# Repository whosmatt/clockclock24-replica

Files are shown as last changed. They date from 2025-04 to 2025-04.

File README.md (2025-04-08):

# clockclock24-replica
DISCLAIMER: All files in this repository are intended for personal use only. All design rights go to Humans Since 1982.

Simple mechanical design for a clockclock24 wall clock compatible with the PCB design by [Vallasc](https://github.com/Vallasc), available here: [clockclock24-replica](https://github.com/Vallasc/clockclock24-replica)  

[3D Preview](clockclock24%20body%20(preview).stl)

## Body
The body is CNC-Milled from a 900x400mm board of 19mm MDF. A frame for wall-mounting and LED ambient lighting is constructed from the same 19mm MDF, cut into different-length strips. The frame is assembled and attached using regular wood glue. 

## PCB attachment
The assembled PCBs are attached using 4 identical 3D-printed spacers each, designed for an ST (self-tapping) 2.9 x 16 metric screw. When using the specified screw, the spacers will self-align the PCBs to the wooden body. 

## Clock arms
The clock arms are 3D-printed and designed to press-fit onto the motor shaft. Slight adjustments to the bore size may be needed to adjust for 3D-printer tolerances. 

## Parts list
| Qty. | Desc. | Stock | Processing |
|-----:|---|---|---|
| 1 | Body | 900x400x19mm MDF  | CNC milling (both sides) |
| 2 | Frame piece (long) | 838x25x19mm MDF | Wood glue |
| 2 | Frame piece (short) | 300x25x19mm MDF | Wood glue |
| 32 | ST 2.9 x 16 metric screw | | |
| 32 | [Spacer](drawings/clockclock24%20spacer.stl) | PLA or comparable | 3D-printing |
| 24 | [Upper hand](drawings/clockclock24%20upper%20hand.stl) | PLA or comparable | 3D-printing |
| 24 | [Lower hand](drawings/clockclock24%20lower%20hand.stl) | PLA or comparable | 3D-printing |

## Photos
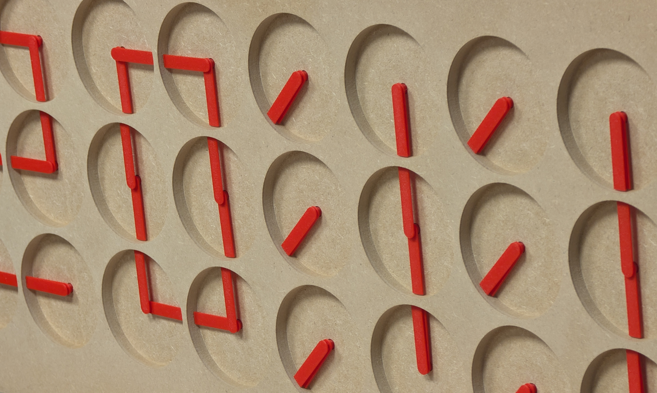
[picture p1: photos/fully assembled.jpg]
Front face of the fully assembled clock

Front face of the clock without arms
Back face of the clock during assembly, with visible spacers
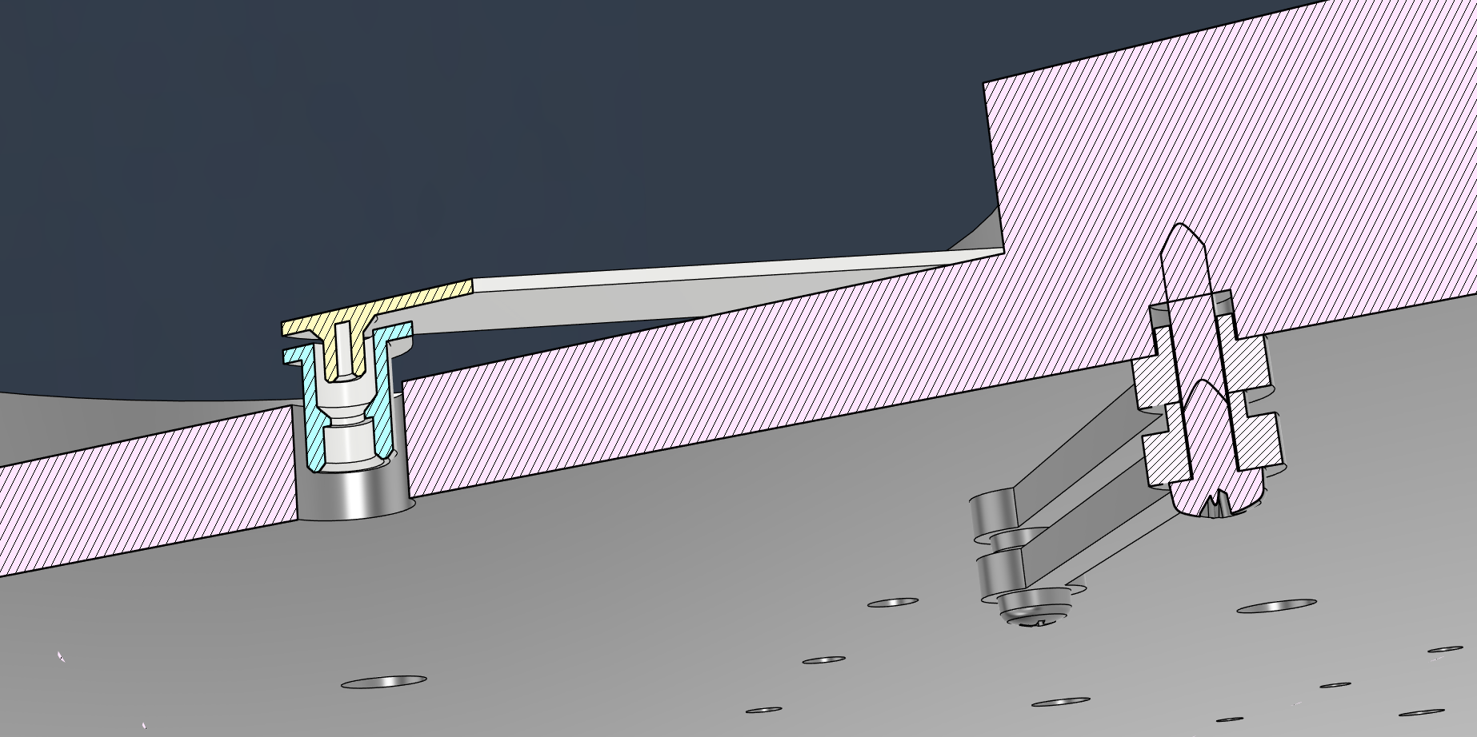
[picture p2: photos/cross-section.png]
Cross section of the clock, showing internal construction of the arms and spacers


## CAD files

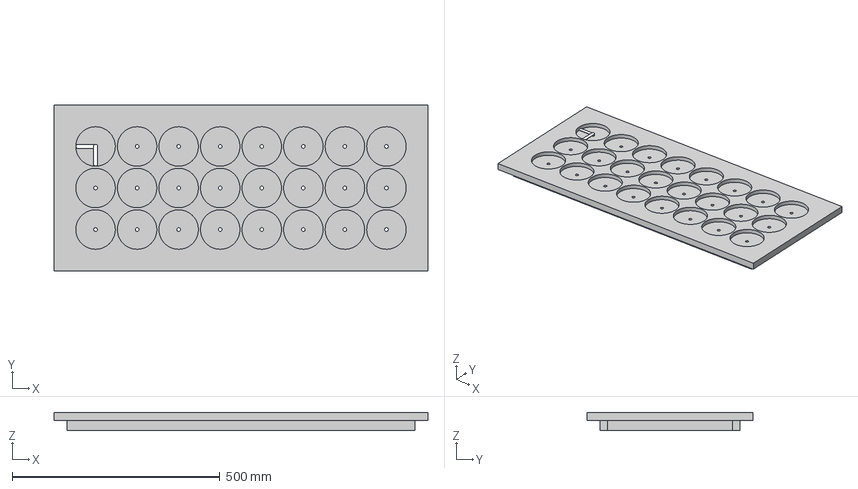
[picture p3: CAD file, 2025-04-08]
drawings/clockclock24 full v14.step
900.0 x 400.0 x 44.0 mm
stepper axle
upper hand
lower hand
spacer x 2
DIN EN ISO 7049 - ST 2.9 x 16 - C - H Steel 4.6 Plain x 2
DIN EN ISO 7049 - ST 2.9 x 6.5 - C - H Steel 4.6 Plain x 2

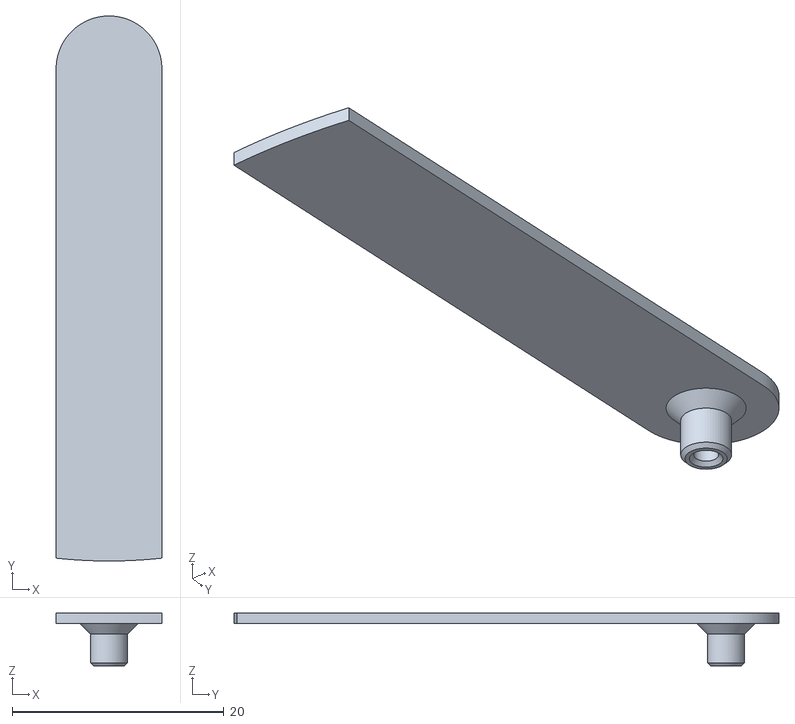
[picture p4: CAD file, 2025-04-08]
drawings/clockclock24 upper hand.stl
10.0 x 51.5 x 5.00

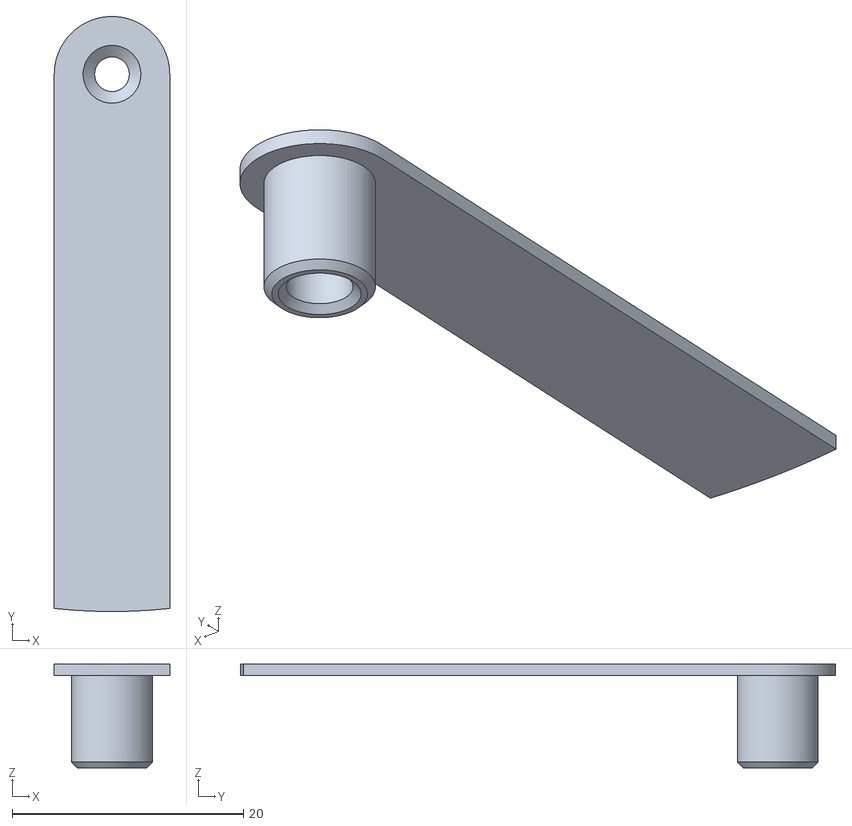
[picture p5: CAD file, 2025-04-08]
drawings/clockclock24 lower hand.stl
10.0 x 51.5 x 9.00

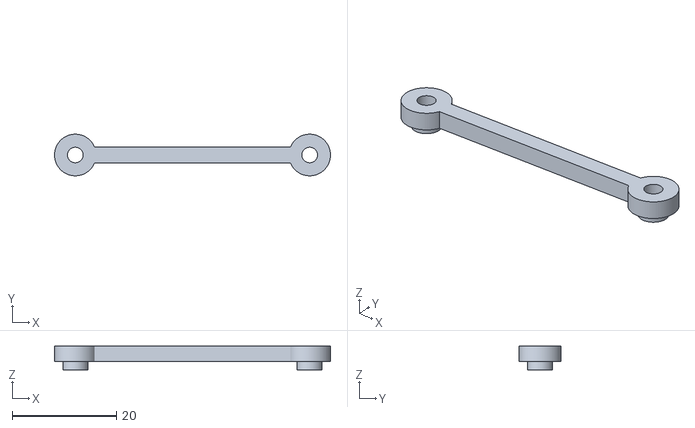
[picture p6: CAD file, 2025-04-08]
drawings/clockclock24 spacer.stl
53.0 x 8.00 x 4.60

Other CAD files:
clockclock24 body (preview).stl
drawings/clockclock24 body Drawing v4 AutoCAD.dwg
drawings/clockclock24 body Drawing v4 Simplified.dwg

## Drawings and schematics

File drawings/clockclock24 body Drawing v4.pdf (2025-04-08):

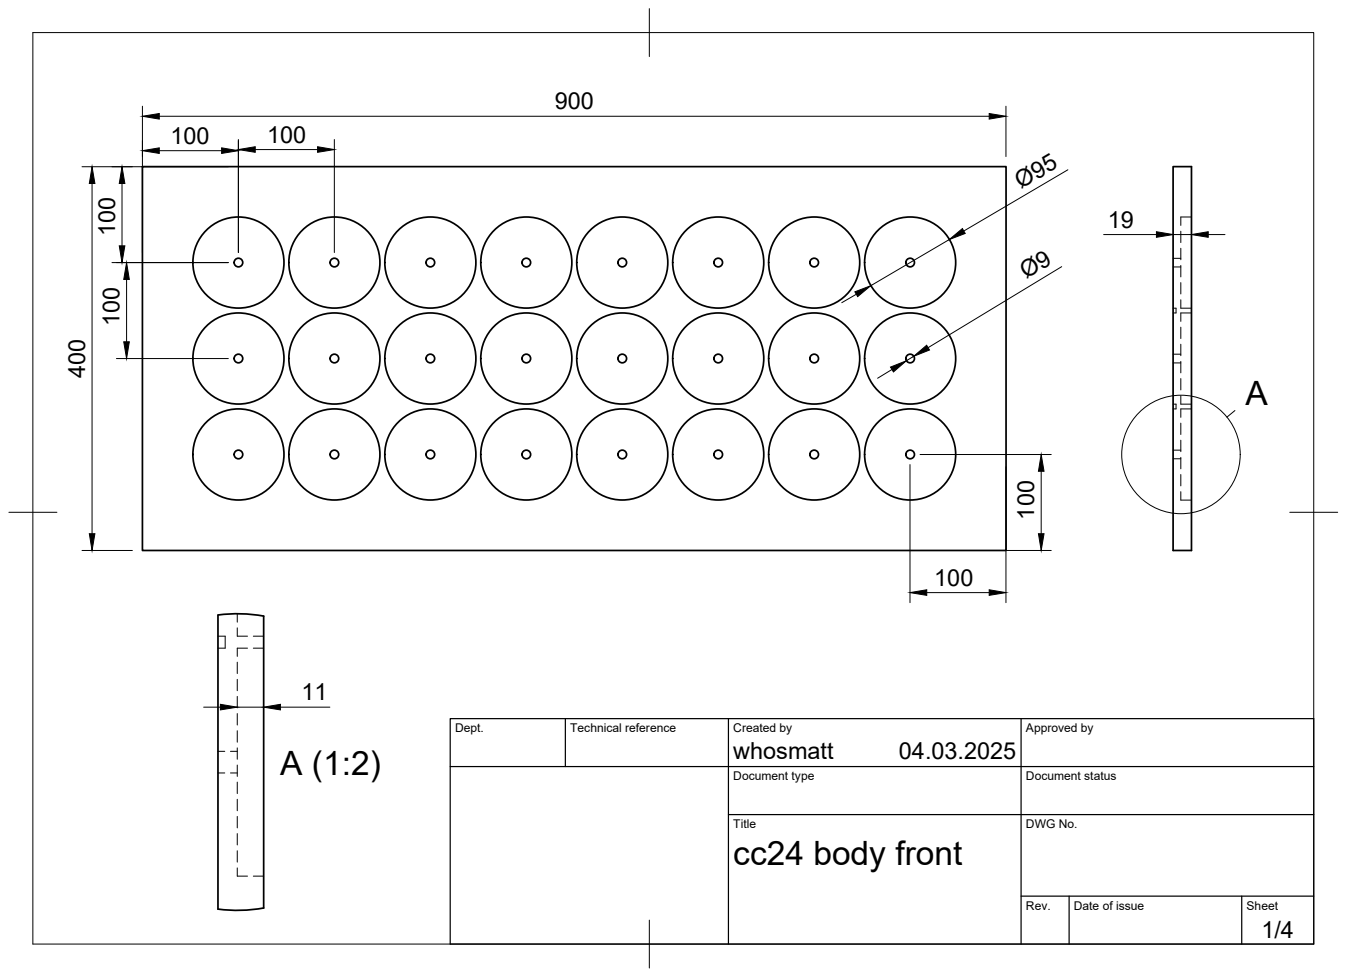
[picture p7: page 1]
whosmatt 400

Dept. | Technical reference | Created by 04.03.2025 | Approved by

Document type | Document status

Title cc24 body front | DWG No.

Rev. | Date of issue | Sheet

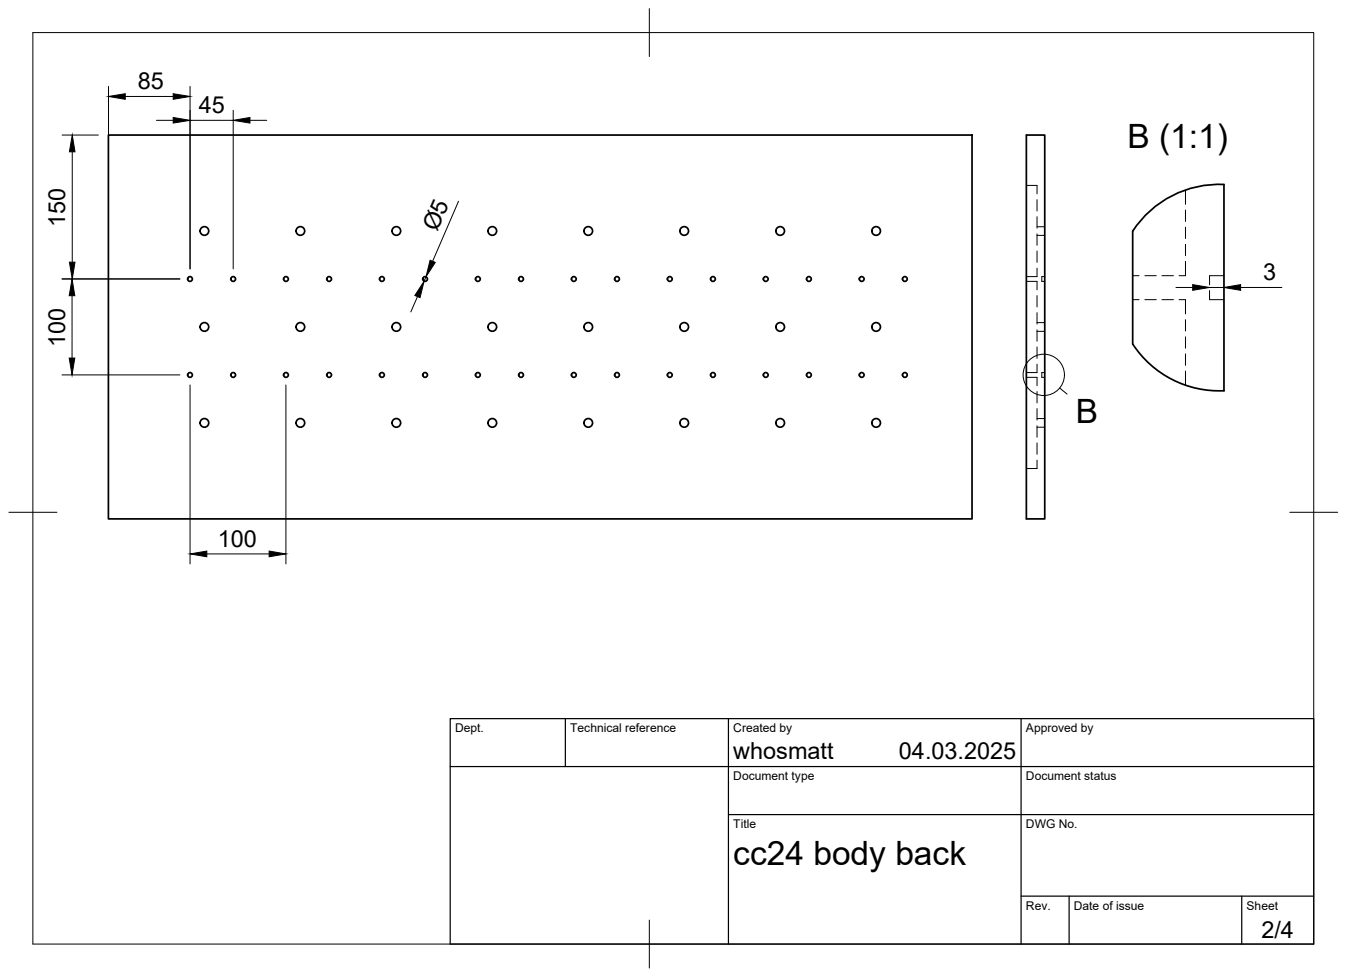
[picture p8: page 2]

Dept. | Technical reference | Created by whosmatt 04.03.2025 | Approved by

Document type | Document status

Title cc24 body back | DWG No.

Rev. | Date of issue | Sheet

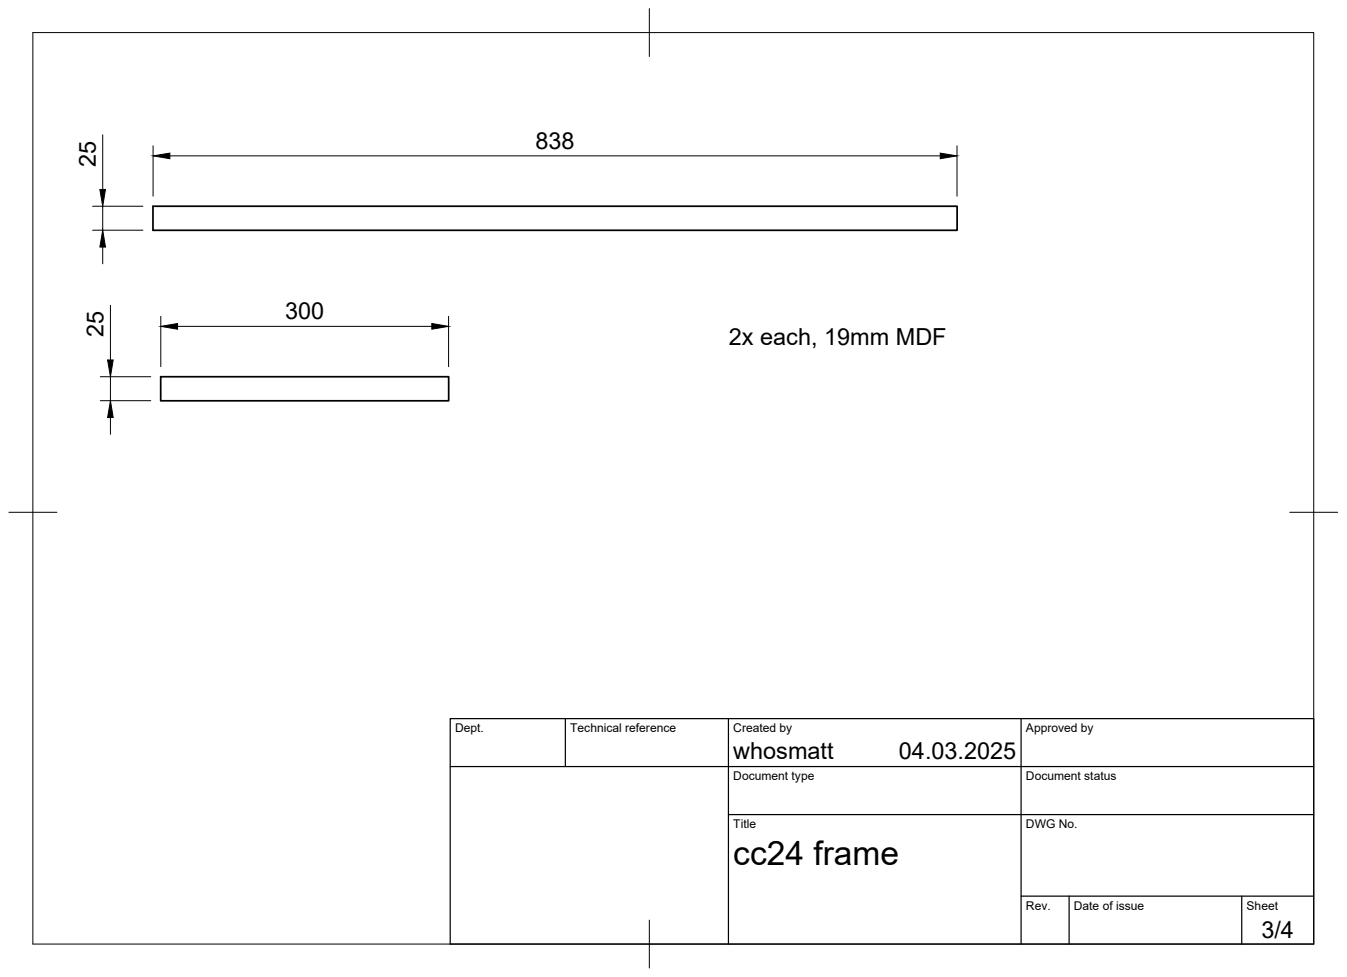
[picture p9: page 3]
whosmatt 25; 2x each, 19mm MDF

Dept. | Technical reference | Created by 04.03.2025 | Approved by

Document type | Document status

Title cc24 frame | DWG No.

Rev. | Date of issue | Sheet

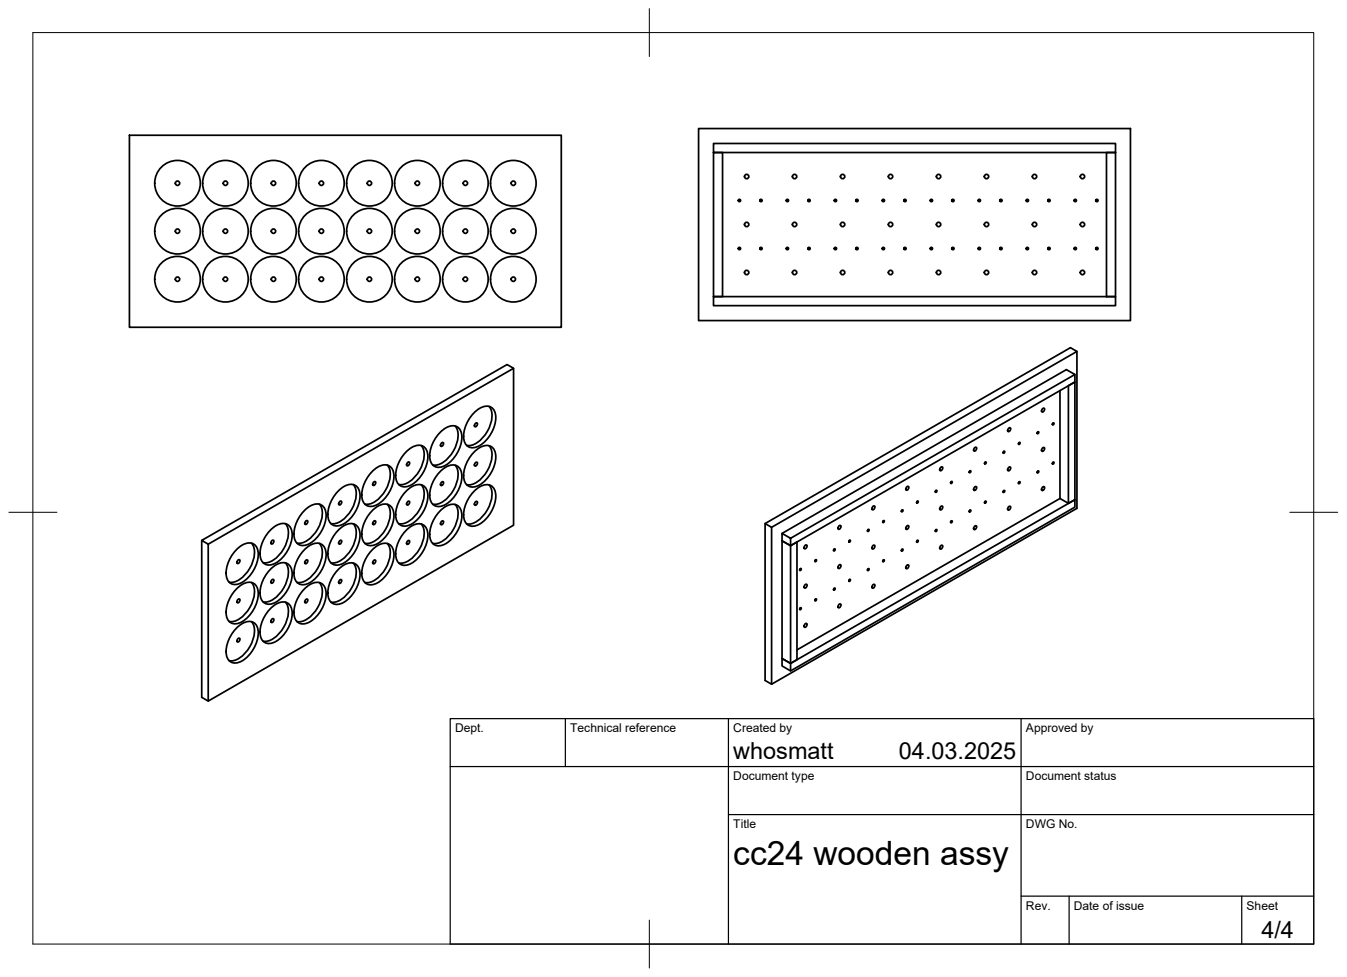
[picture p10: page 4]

Dept. | Technical reference | Created by whosmatt 04.03.2025 | Approved by

Document type | Document status

Title cc24 wooden assy | DWG No.

Rev. | Date of issue | Sheet
